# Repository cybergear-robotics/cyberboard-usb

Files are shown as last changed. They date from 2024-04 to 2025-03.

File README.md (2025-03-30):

# CyberBoard - USB




This is the Kicad project for the CyberBoard. It has an ESP32S3 which is
connected via USB to a computer. The microcontroller drives the cybergear 
motors via CAN. Furthermore a MOLEX CLIK connector is integrated in order
to communicate with the power distribution board [Holybro PM03D Pixhawk 5X Power
Module](https://docs.holybro.com/power-module-and-pdb/power-module/digital-power-module-pm-setup).
This board does not only provides six XT-30 connectors for each cybergear motor,
but also an INA226 i2c power monitor unit. The IMU ICM20948 is integrated on the
CyberBoard.

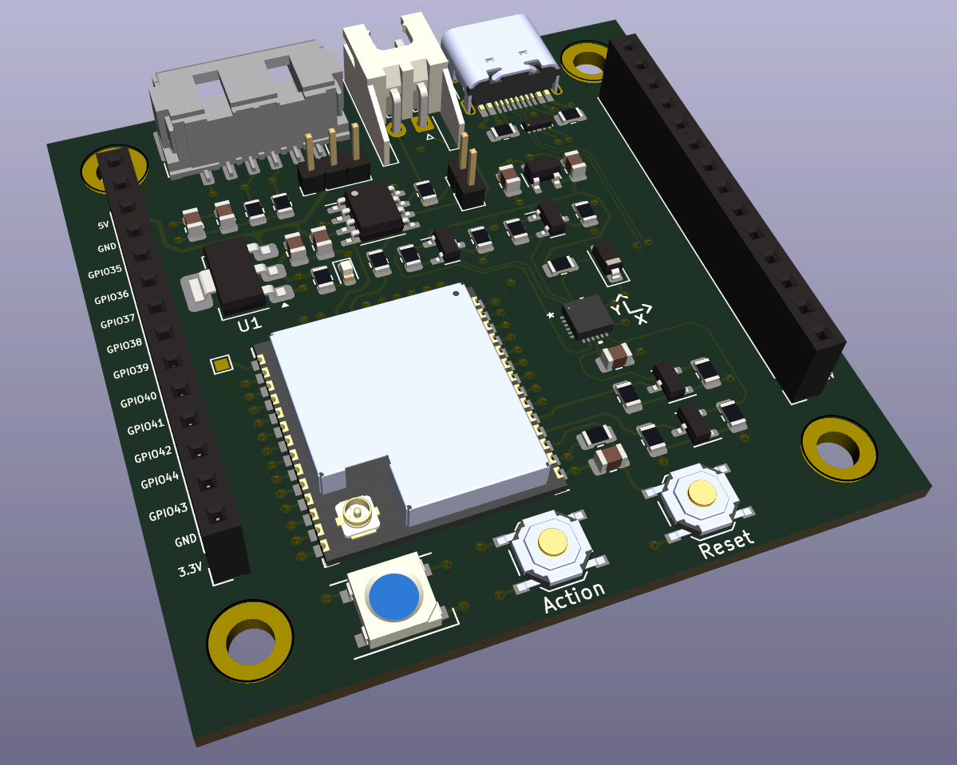
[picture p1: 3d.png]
3D

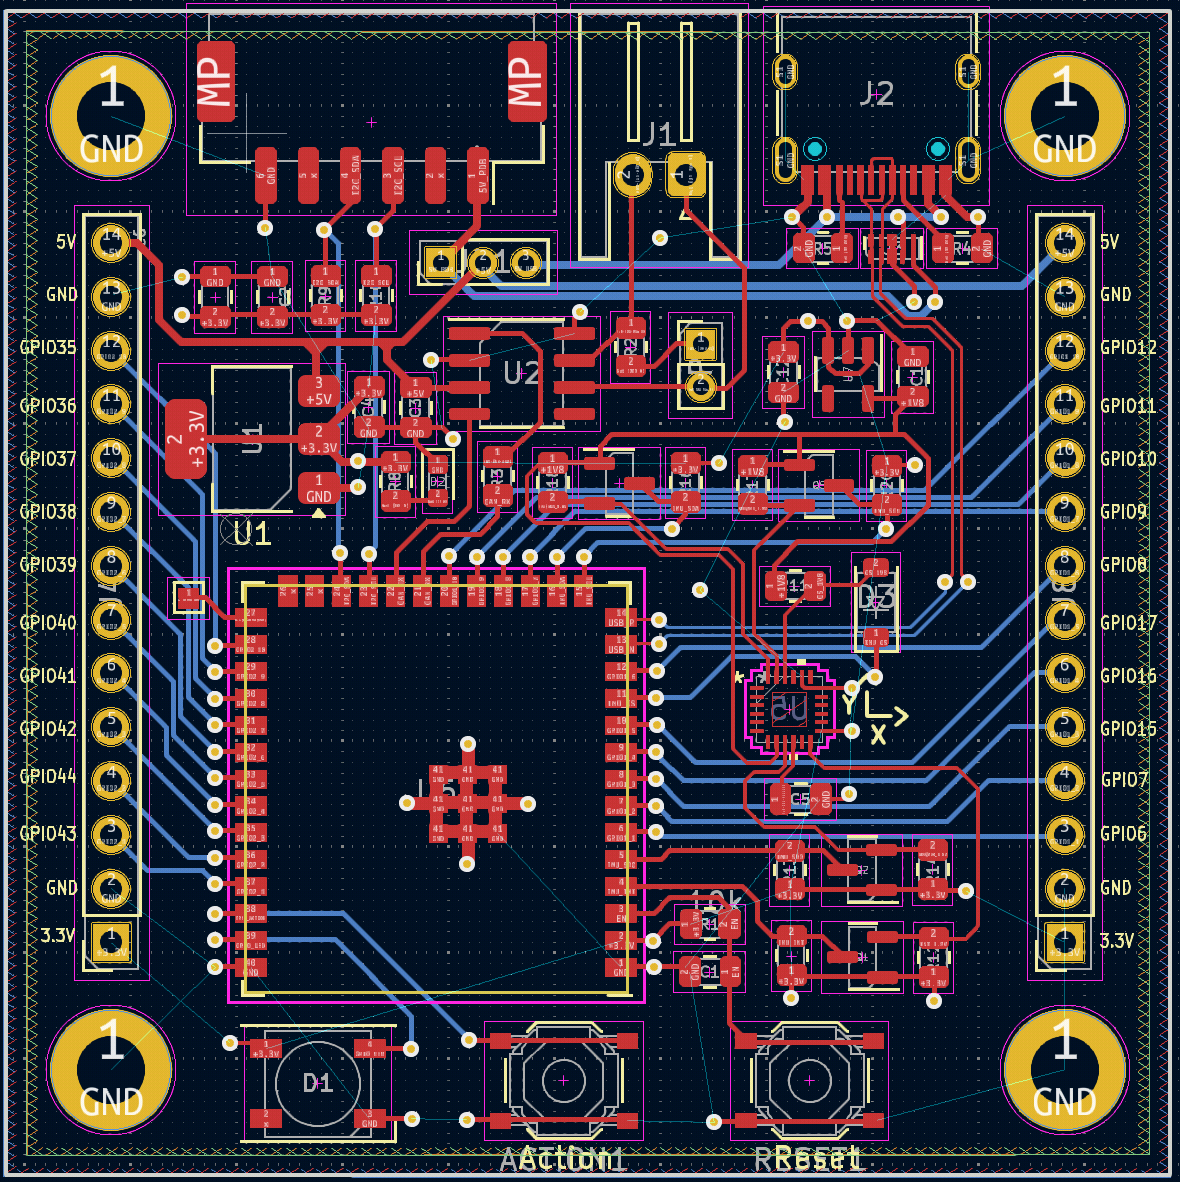
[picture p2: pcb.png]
PCB


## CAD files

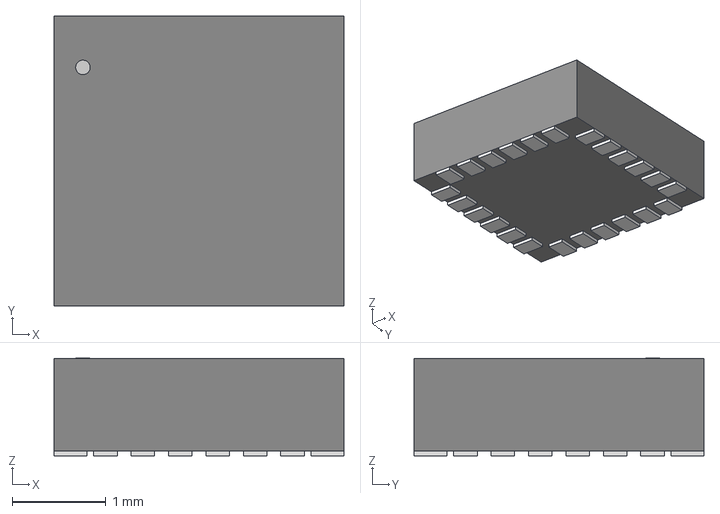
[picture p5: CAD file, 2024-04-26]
3dmodels/QFN24_3X3X0P9_IVS.step
3.10 x 3.10 x 1.04 mm

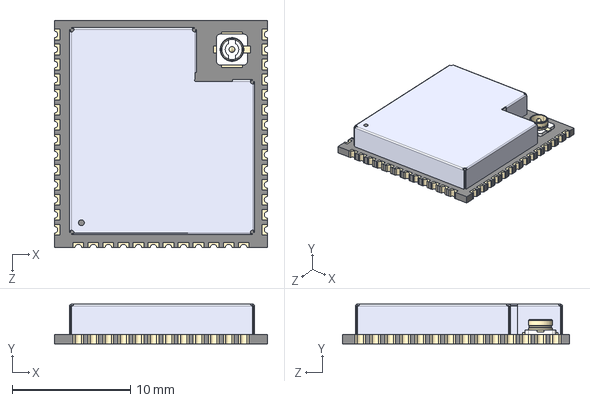
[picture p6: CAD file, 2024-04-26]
3dmodels/ESP32-S3-WROOM-1U-N4.STEP
18.0 x 3.35 x 19.2 mm

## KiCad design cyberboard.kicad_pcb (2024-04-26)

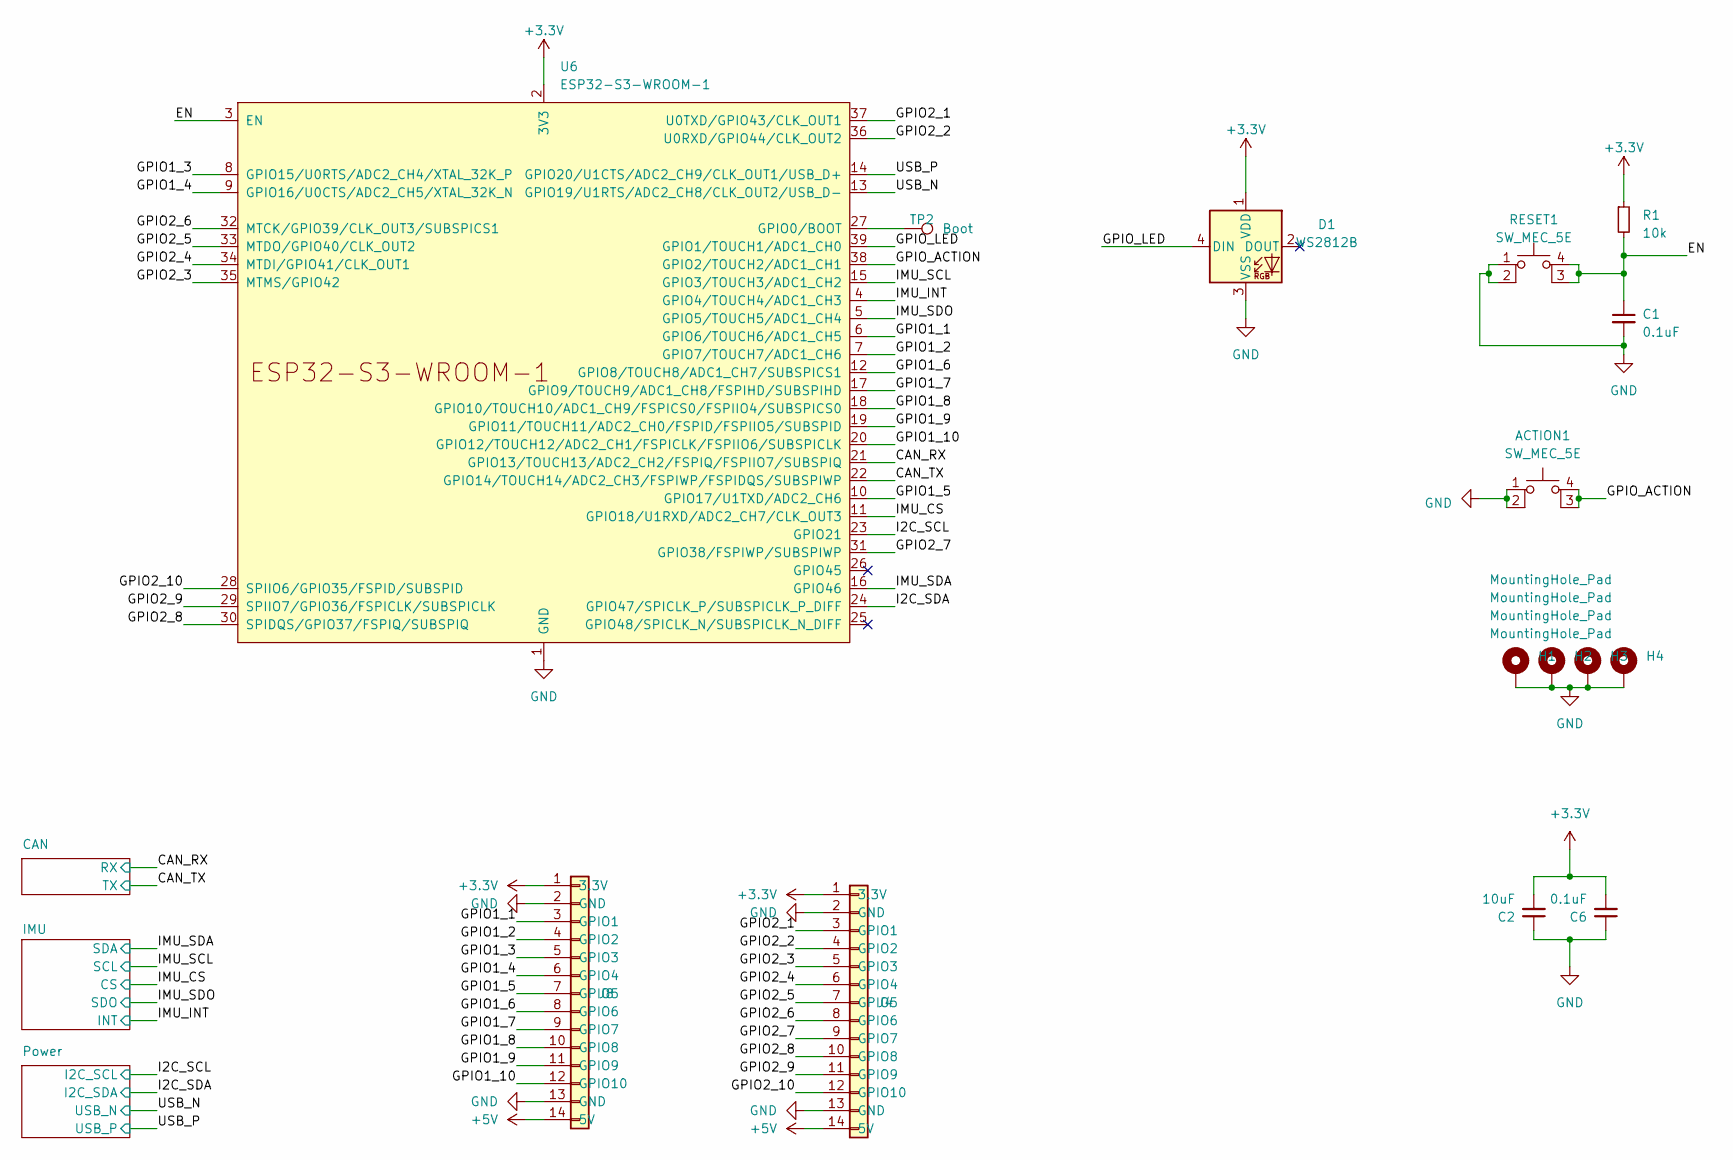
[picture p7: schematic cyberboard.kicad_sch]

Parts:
ACTION1: SW_MEC_5E; SW_Push_1P1T_XKB_TS-1187A; LCSC C318884
C1, C6: 0.1uF; C_0805_2012Metric; LCSC C49678
C2: 10uF; C_0805_2012Metric; LCSC C15850
D1: WS2812B; LED_WS2812B_PLCC4_5.0x5.0mm_P3.2mm
H1, H2, H3, H4: MountingHole_Pad; MountingHole_3.2mm_M3_DIN965_Pad
J4, J8: Conn_01x14; PinSocket_1x14_P2.54mm_Vertical
R1: 10k; R_0805_2012Metric; LCSC C17414
RESET1: SW_MEC_5E; SW_Push_1P1T_XKB_TS-1187A; LCSC C318884
TP2: Boot; TestPoint_Pad_1.0x1.0mm
U6: ESP32-S3-WROOM-1; ESP32-S3-WROOM-1U

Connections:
+3.3V: C2.2, C6.2, D1.1 (VDD), J4.1 (3.3V), J8.1 (3.3V), R1.1, U6.2 (3V3); also elsewhere on the board
+5V: J4.14 (5V), J8.14 (5V); also elsewhere on the board
/CAN_RX: U6.21 (GPIO13/TOUCH13/ADC2_CH2/FSPIQ/FSPIIO7/S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); also elsewhere on the board
/CAN_TX: U6.22 (GPIO14/TOUCH14/ADC2_CH3/FSPIWP/FSPIDQS/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); also elsewhere on the board
/EN: C1.1, R1.2, RESET1.3 (K), RESET1.4 (A), U6.3 (EN)
/GPIO1_1: J8.3 (GPIO1), U6.6 (GPIO6/TOUCH6/ADC1_CH5)
/GPIO1_2: J8.4 (GPIO2), U6.7 (GPIO7/TOUCH7/ADC1_CH6)
/GPIO1_3: J8.5 (GPIO3), U6.8 (GPIO15/U0RTS/ADC2_CH4/XTAL_32K_P)
/GPIO1_4: J8.6 (GPIO4), U6.9 (GPIO16/U0CTS/ADC2_CH5/XTAL_32K_N)
/GPIO1_5: J8.7 (GPIO5), U6.10 (GPIO17/U1TXD/ADC2_CH6)
/GPIO1_6: J8.8 (GPIO6), U6.12 (GPIO8/TOUCH8/ADC1_CH7/SUBSPICS1)
/GPIO1_7: J8.9 (GPIO7), U6.17 (GPIO9/TOUCH9/ADC1_CH8/FSPIHD/SUBSPIHD)
/GPIO1_8: J8.10 (GPIO8), U6.18 (GPIO10/TOUCH10/ADC1_CH9/FSPICS0/FSPIIO4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)
/GPIO1_9: J8.11 (GPIO9), U6.19 (GPIO11/TOUCH11/ADC2_CH0/FSPID/FSPIIO5/S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)
/GPIO1_10: J8.12 (GPIO10), U6.20 (GPIO12/TOUCH12/ADC2_CH1/FSPICLK/FSPIIO6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)
/GPIO2_1: J4.3 (GPIO1), U6.37 (U0TXD/GPIO43/CLK_OUT1)
/GPIO2_2: J4.4 (GPIO2), U6.36 (U0RXD/GPIO44/CLK_OUT2)
/GPIO2_3: J4.5 (GPIO3), U6.35 (MTMS/GPIO42)
/GPIO2_4: J4.6 (GPIO4), U6.34 (MTDI/GPIO41/CLK_OUT1)
/GPIO2_5: J4.7 (GPIO5), U6.33 (MTDO/GPIO40/CLK_OUT2)
/GPIO2_6: J4.8 (GPIO6), U6.32 (MTCK/GPIO39/CLK_OUT3/SUBSPICS1)
/GPIO2_7: J4.9 (GPIO7), U6.31 (GPIO38/FSPIWP/SUBSPIWP)
/GPIO2_8: J4.10 (GPIO8), U6.30 (SPIDQS/GPIO37/FSPIQ/SUBSPIQ)
/GPIO2_9: J4.11 (GPIO9), U6.29 (SPIIO7/GPIO36/FSPICLK/SUBSPICLK)
/GPIO2_10: J4.12 (GPIO10), U6.28 (SPIIO6/GPIO35/FSPID/SUBSPID)
/GPIO_ACTION: ACTION1.3 (K), ACTION1.4 (A), U6.38 (GPIO2/TOUCH2/ADC1_CH1)
/GPIO_LED: D1.4 (DIN), U6.39 (GPIO1/TOUCH1/ADC1_CH0)
/I2C_SCL: U6.23 (GPIO21); also elsewhere on the board
/I2C_SDA: U6.24 (GPIO47/SPICLK_P/SUBSPICLK_P_DIFF); also elsewhere on the board
/IMU_CS: U6.11 (GPIO18/U1RXD/ADC2_CH7/CLK_OUT3); also elsewhere on the board
/IMU_INT: U6.4 (GPIO4/TOUCH4/ADC1_CH3); also elsewhere on the board
/IMU_SCL: U6.15 (GPIO3/TOUCH3/ADC1_CH2); also elsewhere on the board
/IMU_SDA: U6.16 (GPIO46); also elsewhere on the board
/IMU_SDO: U6.5 (GPIO5/TOUCH5/ADC1_CH4); also elsewhere on the board
/USB_N: U6.13 (GPIO19/U1RTS/ADC2_CH8/CLK_OUT2/USB_D-); also elsewhere on the board
/USB_P: U6.14 (GPIO20/U1CTS/ADC2_CH9/CLK_OUT1/USB_D+); also elsewhere on the board
GND: ACTION1.1, ACTION1.2, C1.2, C2.1, C6.1, D1.3 (VSS), H1.1, H2.1, H3.1, H4.1, J4.2 (GND), J4.13 (GND), J8.2 (GND), J8.13 (GND), RESET1.1, RESET1.2, U6.1 (GND), U6.40 (GND), U6.41 (GND); also elsewhere on the board
unnamed: TP2.1, U6.27 (GPIO0/BOOT)

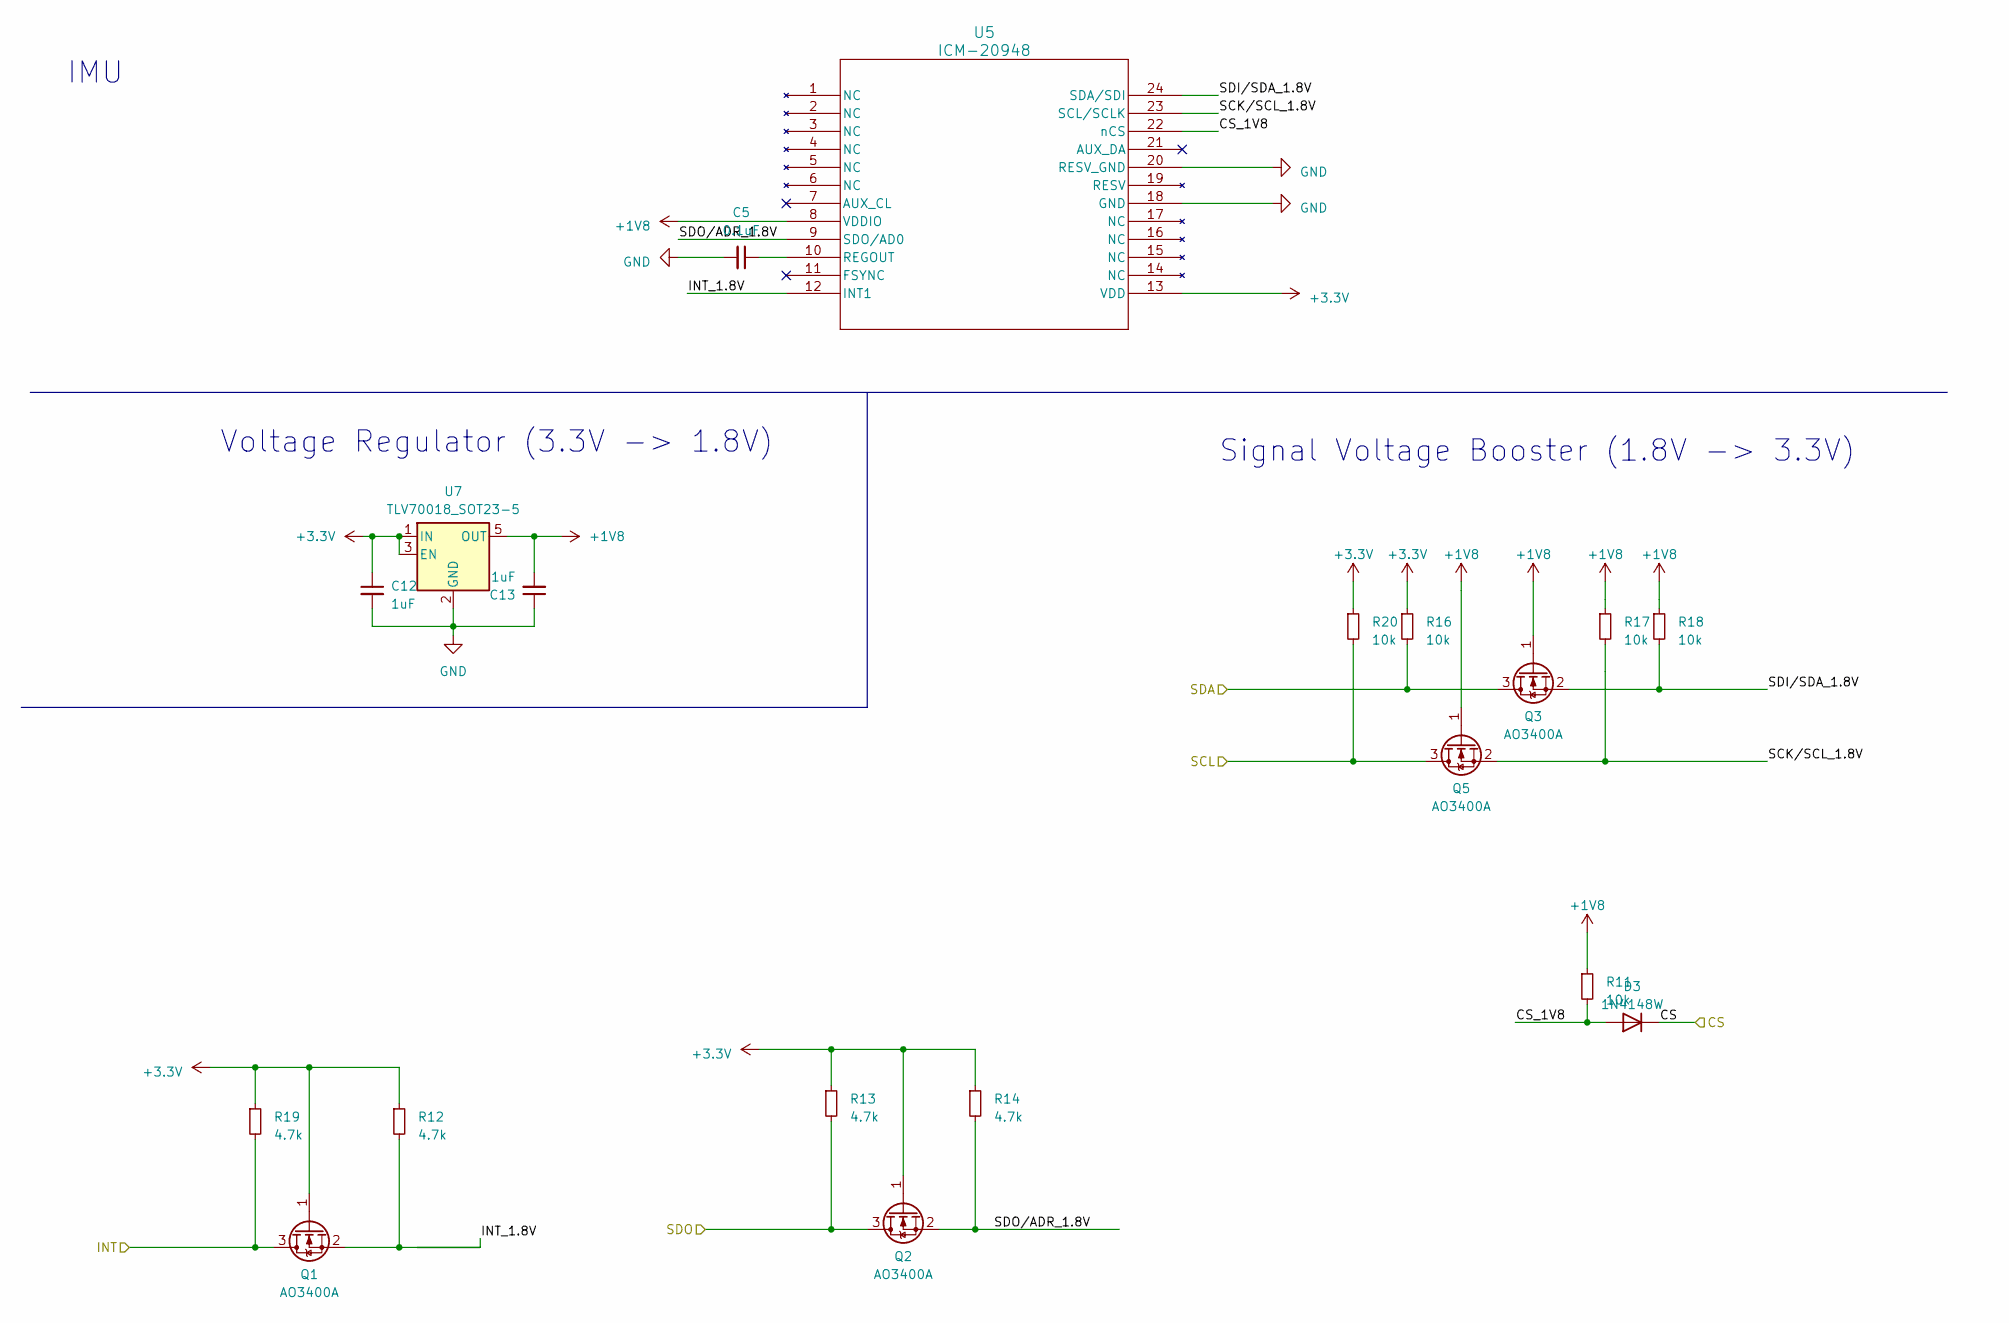
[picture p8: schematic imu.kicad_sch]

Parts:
C5: 0.1uF; C_0805_2012Metric; LCSC C49678
C12, C13: 1uF; C_0805_2012Metric; LCSC C28323
D3: 1N4148W; D_SOD-123; LCSC C81598
Q1, Q2, Q3, Q5: AO3400A; SOT-23; LCSC C20917
R11, R16, R17, R18, R20: 10k; R_0805_2012Metric; LCSC C17414
R12, R13, R14, R19: 4.7k; R_0805_2012Metric; LCSC C17673
U5: ICM-20948; QFN24_3X3X0P9_IVS; LCSC C726001
U7: TLV70018_SOT23-5; SOT-23-5; LCSC C79924

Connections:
+1V8: C13.2, Q3.1 (G), Q5.1 (G), R11.1, R17.1, R18.1, U5.8 (VDDIO), U7.5 (OUT)
+3.3V: C12.1, Q1.1 (G), Q2.1 (G), R12.1, R13.1, R14.1, R16.1, R19.1, R20.1, U5.13 (VDD), U7.1 (IN), U7.3 (EN); also elsewhere on the board
/IMU/CS_1V8: D3.2 (A), R11.2, U5.22 (nCS)
/IMU/INT_1.8V: Q1.2 (S), R12.2, U5.12 (INT1)
/IMU_CS: D3.1 (K); also elsewhere on the board
/IMU_INT: Q1.3 (D), R19.2; also elsewhere on the board
/IMU_SCL: Q5.3 (D), R20.2; also elsewhere on the board
/IMU_SDA: Q3.3 (D), R16.2; also elsewhere on the board
/IMU_SDO: Q2.3 (D), R13.2; also elsewhere on the board
GND: C5.2, C12.2, C13.1, U5.18 (GND), U5.20 (RESV_GND), U7.2 (GND); also elsewhere on the board
unnamed: C5.1, U5.10 (REGOUT)

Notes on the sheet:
IMU
Signal Voltage Booster (1.8V -> 3.3V)
Voltage Regulator (3.3V -> 1.8V)

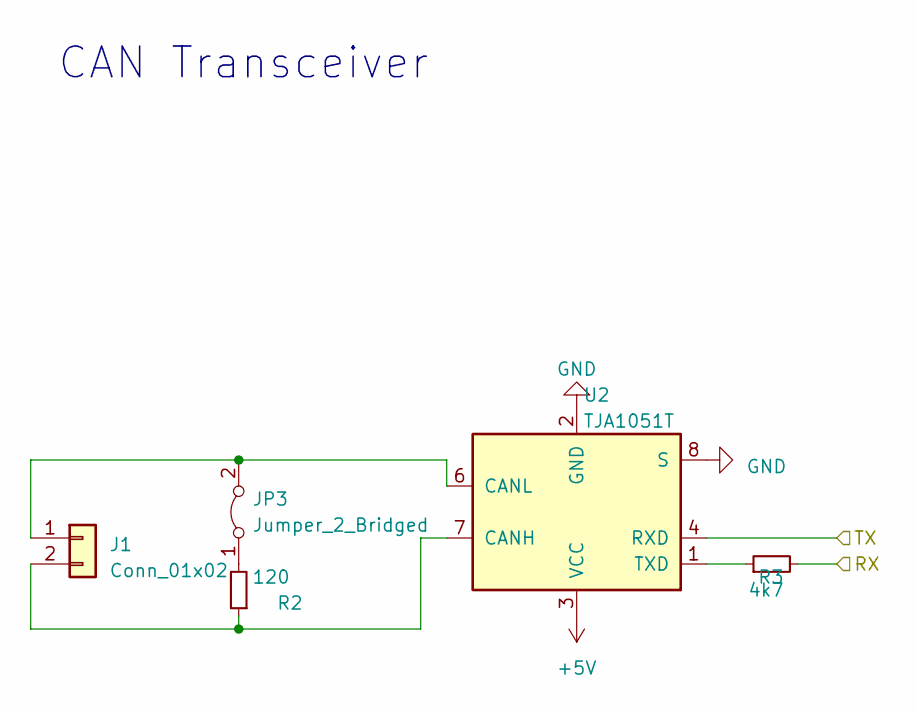
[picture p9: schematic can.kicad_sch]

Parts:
J1: Conn_01x02; JST_XH_S2B-XH-A-1_1x02_P2.50mm_Horizontal
JP3: Jumper_2_Bridged; PinHeader_1x02_P2.00mm_Vertical
R2: 120; R_0805_2012Metric; LCSC C17437
R3: 4k7; R_0805_2012Metric; LCSC C17673
U2: TJA1051T; SOIC-8_3.9x4.9mm_P1.27mm; LCSC C92211

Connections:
+5V: U2.3 (VCC); also elsewhere on the board
/CAN_RX: R3.2; also elsewhere on the board
/CAN_TX: U2.4 (RXD); also elsewhere on the board
GND: U2.2 (GND), U2.8 (S); also elsewhere on the board
unnamed: J1.1, JP3.2 (B), U2.6 (CANL)
unnamed: J1.2, R2.1, U2.7 (CANH)
unnamed: JP3.1 (A), R2.2
unnamed: R3.1, U2.1 (TXD)

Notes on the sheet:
CAN Transceiver

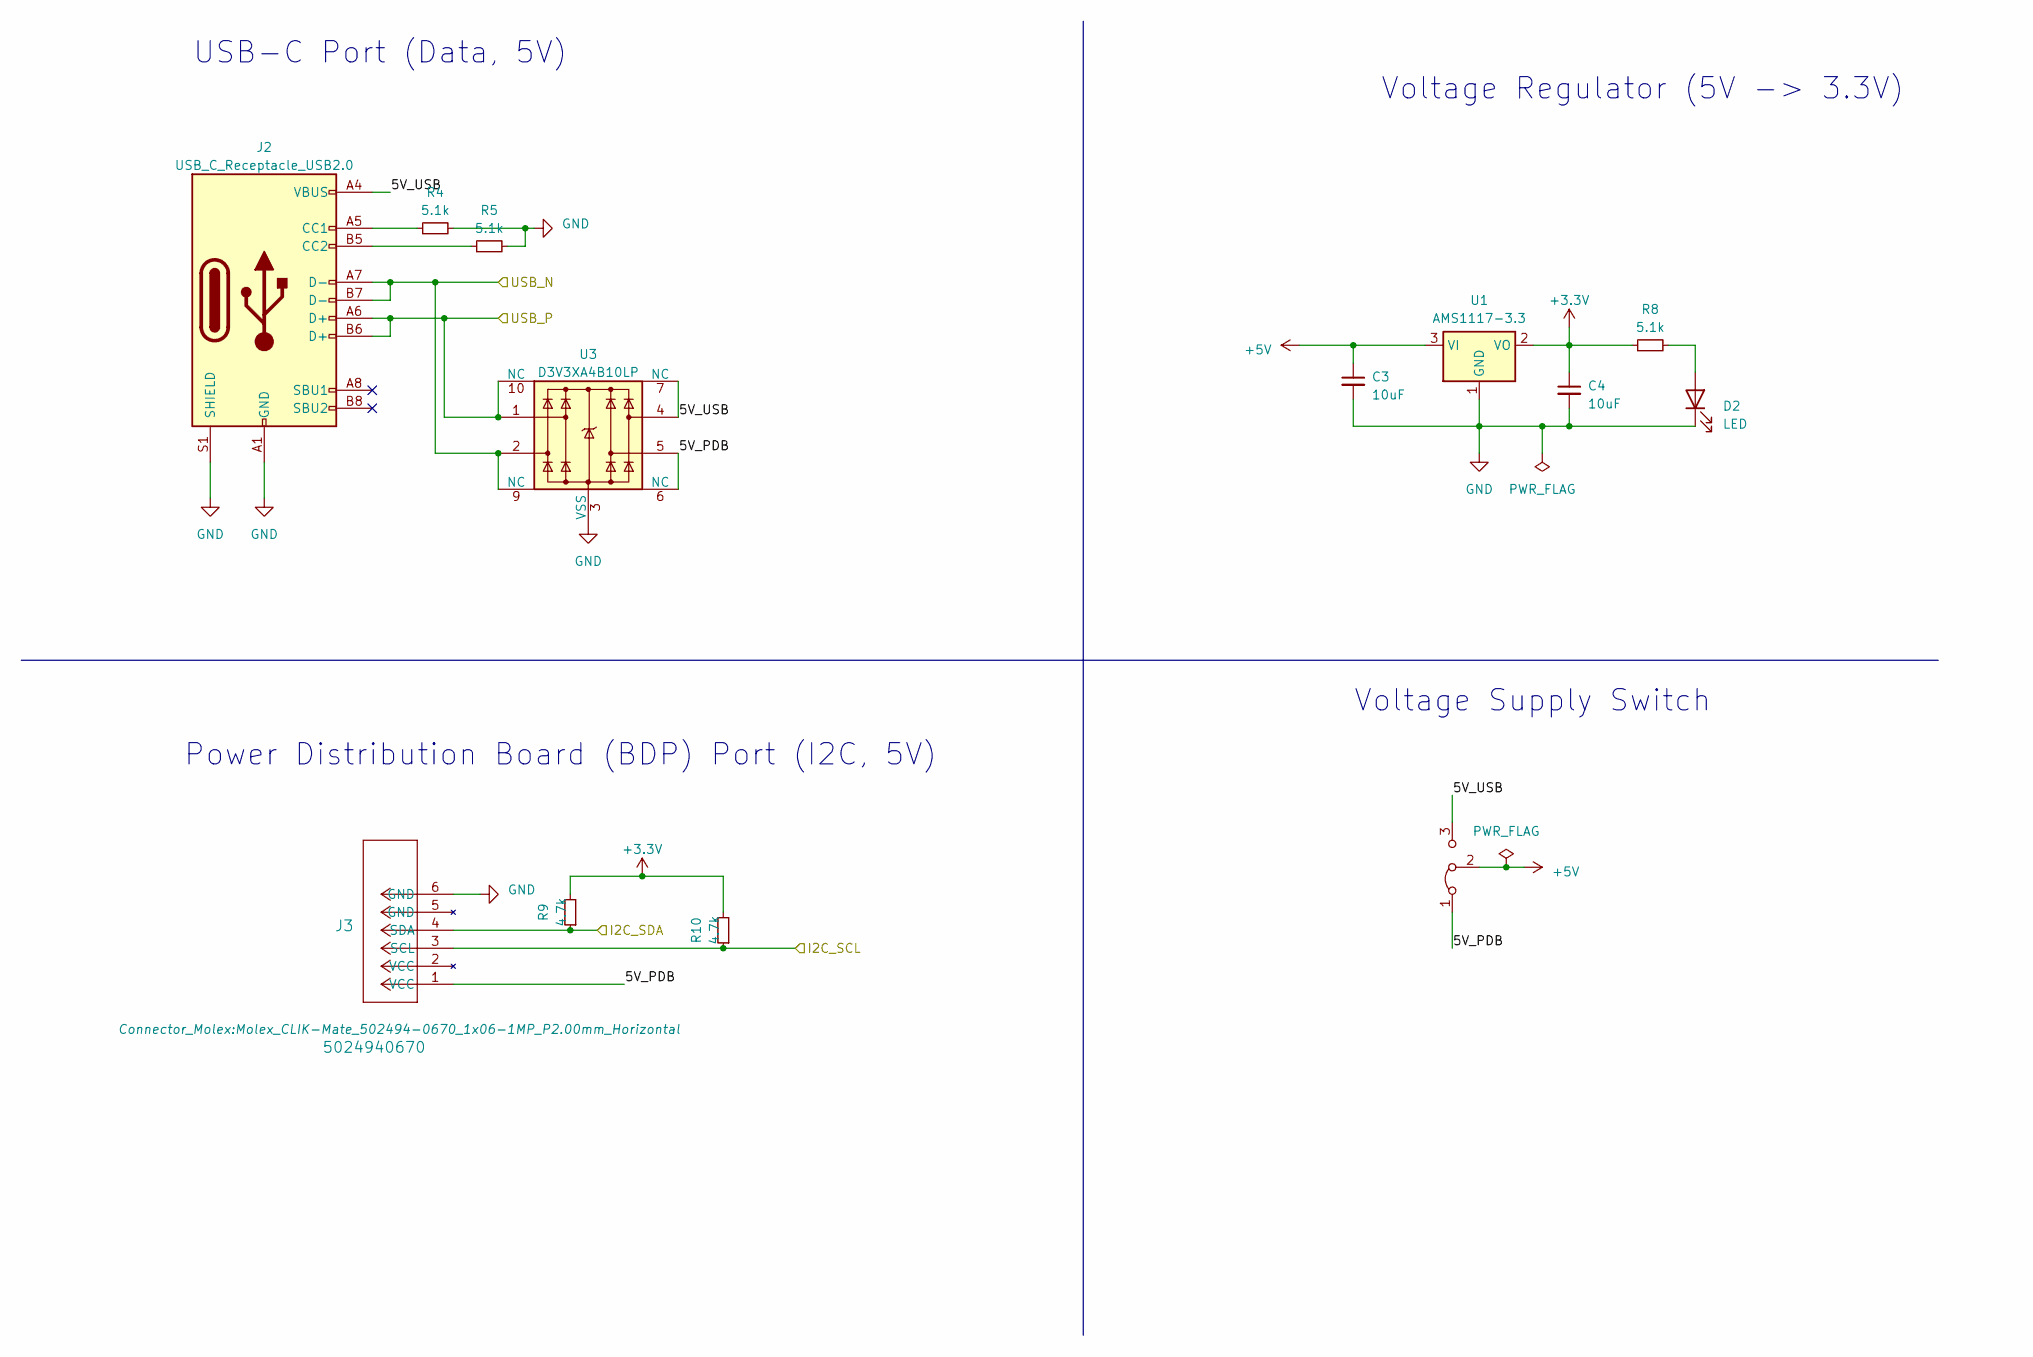
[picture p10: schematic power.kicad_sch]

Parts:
C3, C4: 10uF; C_0805_2012Metric; LCSC C15850
D2: LED; LED_0603_1608Metric; LCSC C2286
J2: USB_C_Receptacle_USB2.0; USB_C_Receptacle_HRO_TYPE-C-31-M-12; LCSC C165948
J3: 5024940670; Molex_CLIK-Mate_502494-0670_1x06-1MP_P2.00mm_Horizontal; LCSC C587930
JP1: Jumper_3_Bridged12; PinHeader_1x03_P2.00mm_Vertical
R4, R5, R8: 5.1k; R_0805_2012Metric; LCSC C27834
R9, R10: 4.7k; R_0805_2012Metric; LCSC C17673
U1: AMS1117-3.3; SOT-223-3_TabPin2; LCSC C6186
U3: D3V3XA4B10LP; Diodes_UDFN-10_1.0x2.5mm_P0.5mm; LCSC C1980462

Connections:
+3.3V: C4.1, R8.1, R9.2, R10.2, U1.2 (VO); also elsewhere on the board
+5V: C3.1, JP1.2 (C), U1.3 (VI); also elsewhere on the board
/I2C_SCL: J3.3 (SCL), R10.1; also elsewhere on the board
/I2C_SDA: J3.4 (SDA), R9.1; also elsewhere on the board
/Power/5V_PDB: J3.1 (VCC), JP1.1 (A), U3.5, U3.6 (NC)
/Power/5V_USB: J2.A4 (VBUS), J2.A9 (VBUS), J2.B4 (VBUS), J2.B9 (VBUS), JP1.3 (B), U3.4, U3.7 (NC)
/USB_N: J2.A7 (D-), J2.B7 (D-), U3.2, U3.9 (NC); also elsewhere on the board
/USB_P: J2.A6 (D+), J2.B6 (D+), U3.1, U3.10 (NC); also elsewhere on the board
GND: C3.2, C4.2, D2.1 (K), J2.A1 (GND), J2.A12 (GND), J2.B1 (GND), J2.B12 (GND), J2.S1 (SHIELD), J3.6 (GND), R4.2, R5.2, U1.1 (GND), U3.3 (VSS), U3.8 (VSS); also elsewhere on the board
unnamed: D2.2 (A), R8.2
unnamed: J2.A5 (CC1), R4.1
unnamed: J2.B5 (CC2), R5.1

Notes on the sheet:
USB-C Port (Data, 5V)
Voltage Regulator (5V -> 3.3V)
Power Distribution Board (BDP) Port (I2C, 5V)
Voltage Supply Switch

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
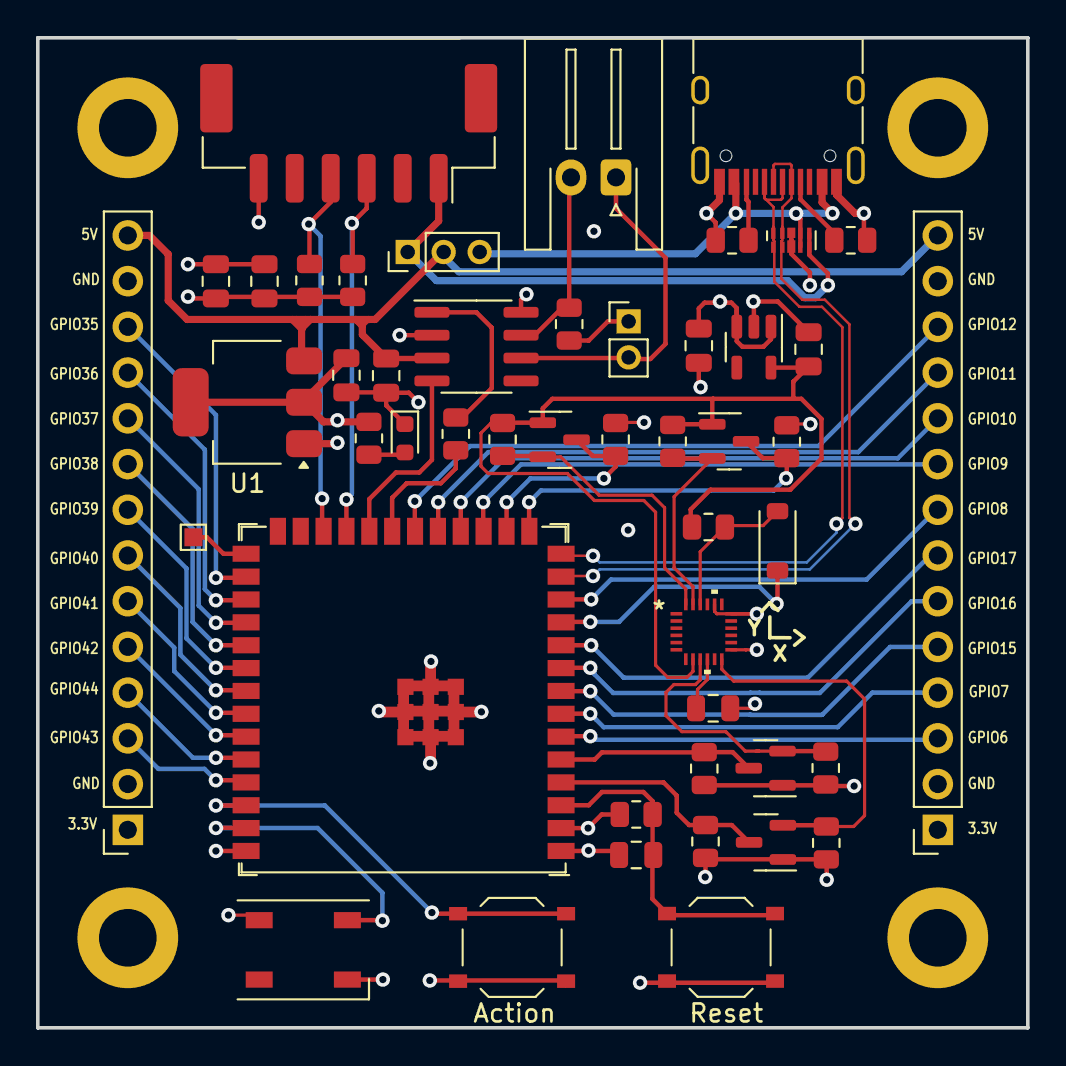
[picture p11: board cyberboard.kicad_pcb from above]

Board: 4 copper layers, 55.0 x 55.0 mm, 52 parts (0 on the bottom side), 54 nets.

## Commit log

2024-04-26 deployment release
    [BOM-cyberboard.csv, ESP32-S3-WROOM-1U-N4.STEP, QFN24_3X3X0P9_IVS.step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]
2025-03-30 add small changes
    [can.kicad_sch, cyberboard.kicad_sch, imu.kicad_sch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]
2025-03-30 remove release files
    [BOM-cyberboard.csv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]

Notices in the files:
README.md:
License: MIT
